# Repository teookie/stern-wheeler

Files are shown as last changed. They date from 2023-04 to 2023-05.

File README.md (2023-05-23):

# stern-wheeler
Filament buffer for multi-material FDM 3D printers

Special Note:
I have uploaded the Stern-Wheeler to printables. This github will remain and I will keep it updated. Please consider downloading from printables however, as I do enjoy earning free prusament. :-) The mini and mega sizes will not be available here and will only be available on printables.

Thank you to everyone who gave feedback and helped with development!

https://www.printables.com/model/472316-stern-wheeler

Change log:
5/22/2023
- Centered bearings in the wheel. The wheel should be (slightly) more stable
- Added a pic of a loaded 6 lane stern-wheeler to PICs folder
- Added parts for a 9 lane version to printables. This has not been tested by me. Keep in mind that more lanes means more friction.

5/10/2023
- Lengthened axel to interface with a pocket added to the cover, and enlarged the spacer to fit around the axel. This improves wheel alignment during assembly, and makes the wheel installation more robust. See section view added to pics below. (I had a situation where the filament spool got jammed causing the extruder to pull the filament hard enough to misalign the wheel. This change is meant to prevent this.)
- Remodeled the wheel-mount so that it overlaps the joint between lane #1 and the wheel. This will prevent the thin wall of lane 1 from deflecting and making a gap where filament can escape.
- Added embossed "F" and "B" to the front and back of the wheel to aid during installation.
- Reversed wheel print orientation - it now prints on it's front face instead of the back face. This prevents possible wheel misalignment caused by drooping filament in the bearing pocket bridges.

To update an existing stern-wheeler with these improvements, print and install the following parts:
- wheel-mount
- axel
- spacer
- cover

5/6/2023
- Published these files at printables.com
- Added mini and mega sizes to printables
- Removed assembly instructions and replaced with an exploded view (a picture is worth 1000 words)

5/4/2023
- Removed ridges from wheel and added scallops. Greatly reduces wheel friction.
- Added a notch to the wheel for the print seam. Make sure your slicer takes advantage! Reduces wheel friction.
- Loosened fit of pins slightly to prevent lane cracking during assembly. 
- Reduced thru hole diameter for 5mm fasteners on axel. Positions wheel more accurately during assembly.
- Rolled back increased clearance between lanes and wheel from 4/7 update. Not needed with new wheel design.

4/7/2023
- Oriented stl's for printing
- Lengthened pins and added matching recesses to clamps, mount, and wheel mount. Should help with wheel alignment during assembly.
- Increased clearance between lanes and wheel by 0.1mm
- Added hex feature to axle that recesses into the wheel mount. Should make assembly easier.
- Removed material from bottom of wheel to make wheel alignment easier
- Made filament path "ambidextrous" so either side can be the inlet or outlet
- Added BOM
- Added written printing and assembly instructions to this readme

BOM
- 2x 608 Bearings
- 12x M3 heatset inserts
- 12x M3x8 or M3x10 cap screws
- 2x M5x16 button head screws
- about 700g of filament (for a 6 lane standard size buffer in ABS)

Printing instructions:
- Designed to be printed with ABS. If you mix materials make sure that they have equal amount of shrinkage or your wheel might not fit!
- 2 perimeters, 15% infill for wheel
- 4 perimeters, 40% infill for everything else

Assembly instructions:
1) See exploded view. ;-)

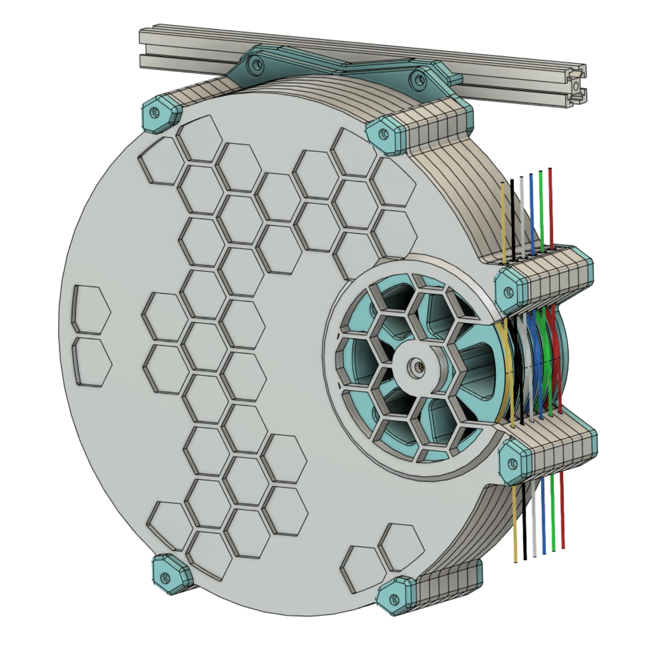
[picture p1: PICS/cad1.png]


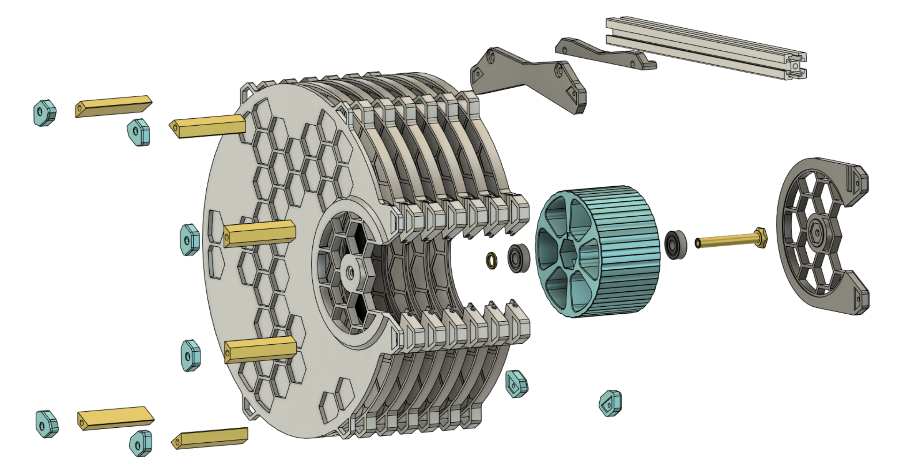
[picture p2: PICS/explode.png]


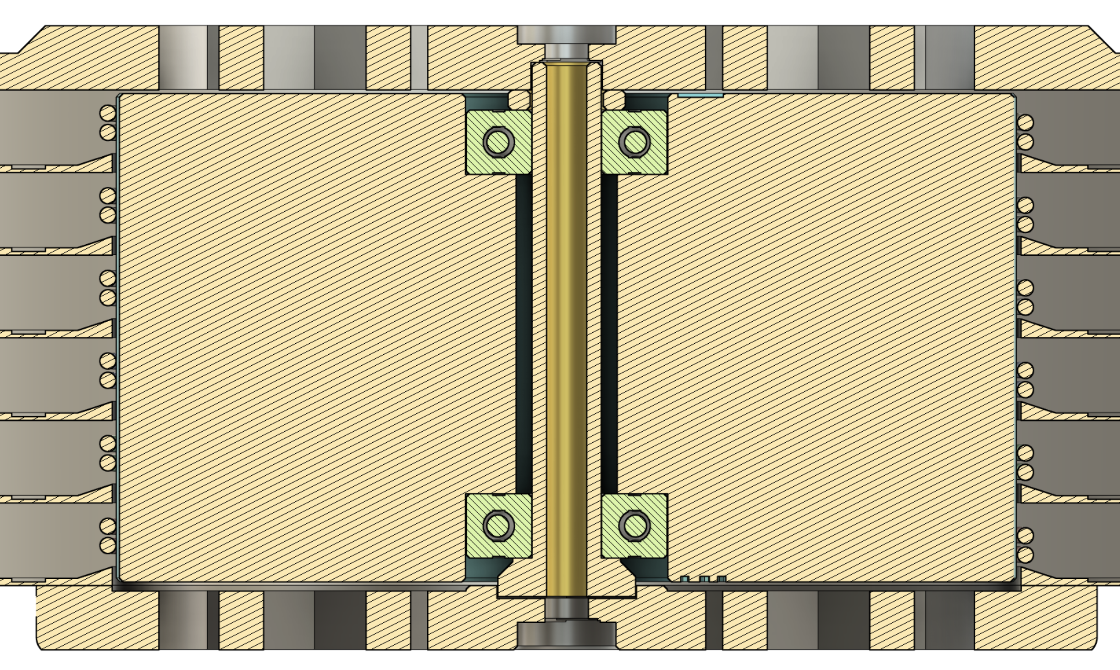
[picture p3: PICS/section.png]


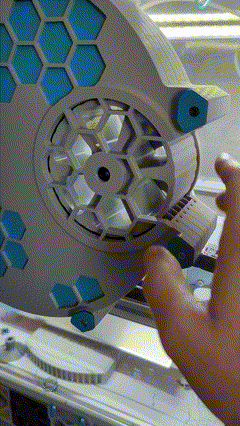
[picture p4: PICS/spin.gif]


https://youtube.com/shorts/Z2WNvIMlSTY?feature=share

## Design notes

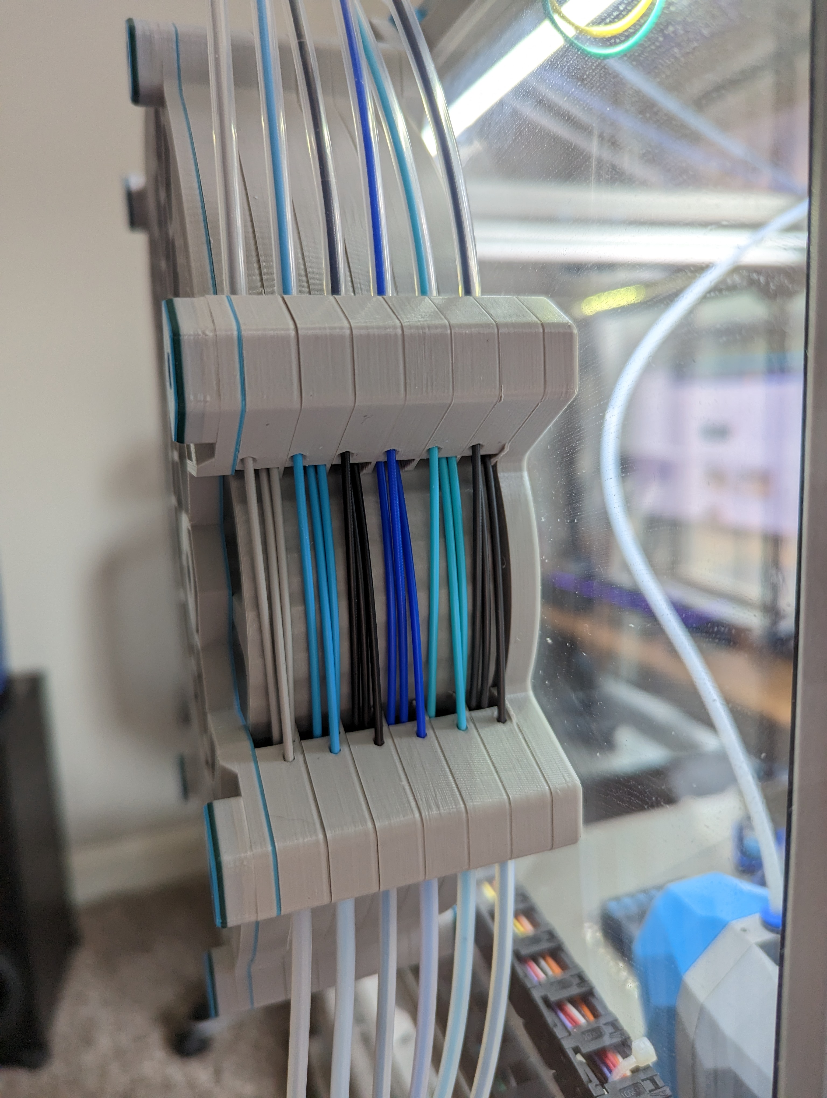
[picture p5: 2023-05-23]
PICS/loaded.jpg

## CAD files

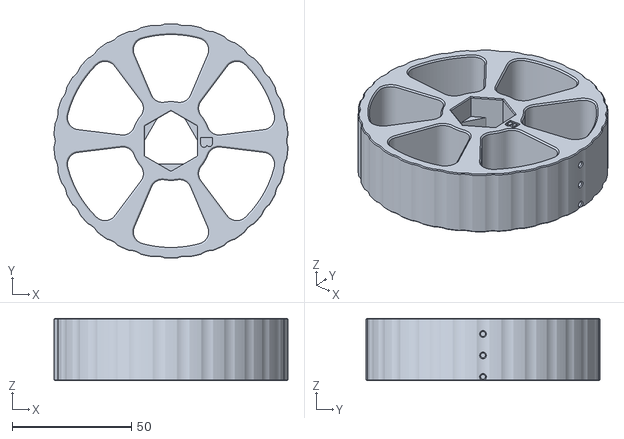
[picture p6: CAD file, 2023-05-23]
STLs/EXPERIMENTAL-tpu-wheel.stl
98.1 x 98.2 x 26.2

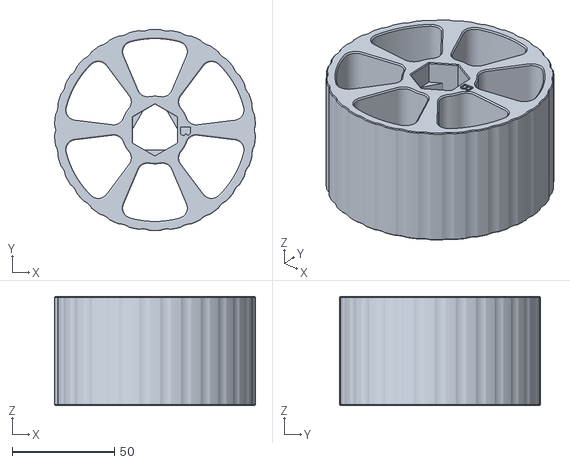
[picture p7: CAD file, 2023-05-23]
STLs/wheel.stl
98.1 x 98.2 x 53.2

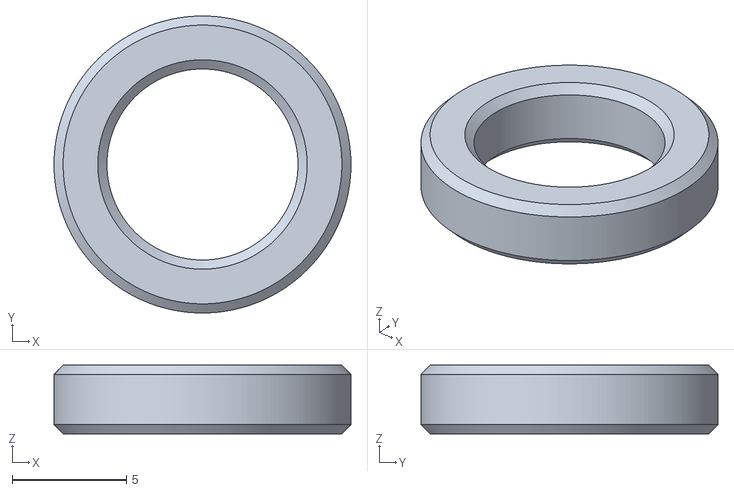
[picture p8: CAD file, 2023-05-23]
STLs/spacer.stl
13.0 x 13.0 x 3.00

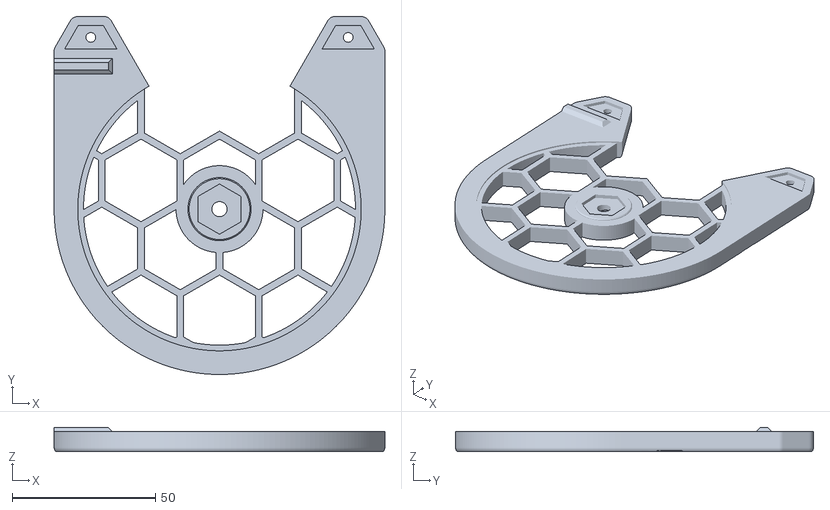
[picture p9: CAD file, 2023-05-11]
STLs/wheel_mount.stl
115.6 x 125.1 x 8.40

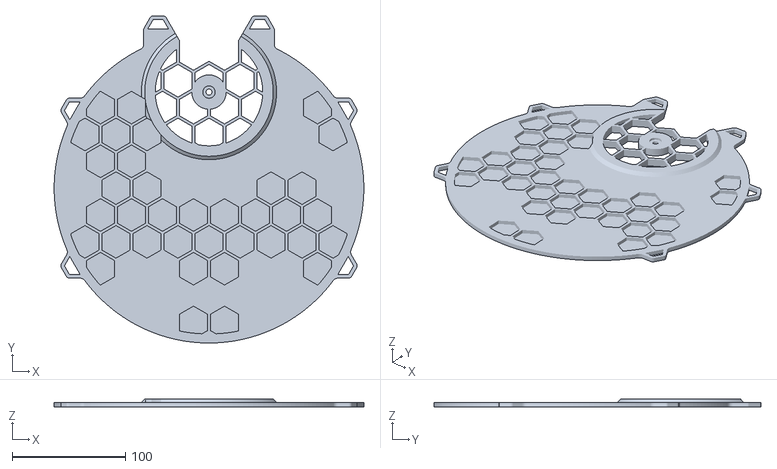
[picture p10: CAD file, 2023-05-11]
STLs/cover.stl
274.0 x 289.3 x 7.00

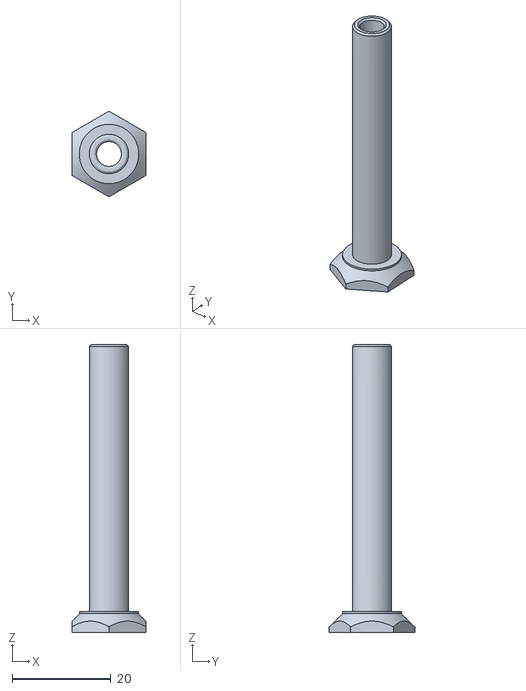
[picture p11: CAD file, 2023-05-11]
STLs/axel.stl
15.0 x 17.3 x 58.2

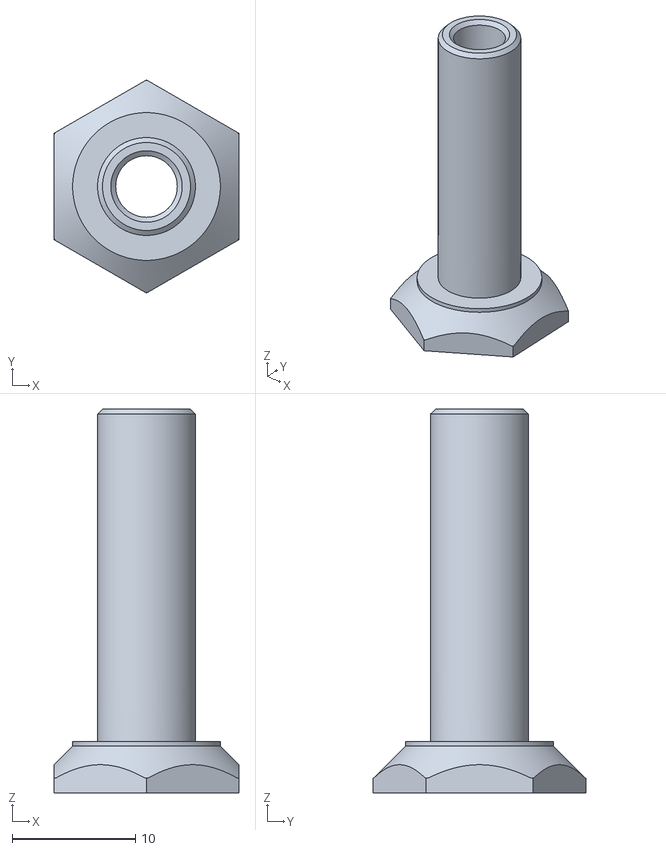
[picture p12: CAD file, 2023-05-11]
STLs/3-lane axel.stl
15.0 x 17.3 x 31.2

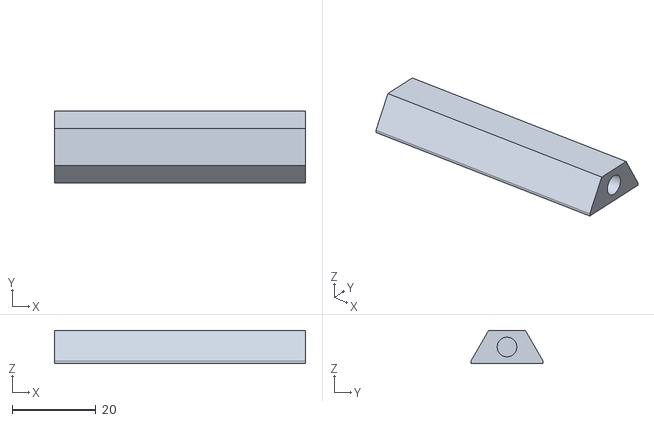
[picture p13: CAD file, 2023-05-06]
STLs/pin.stl
60.0 x 17.3 x 8.00

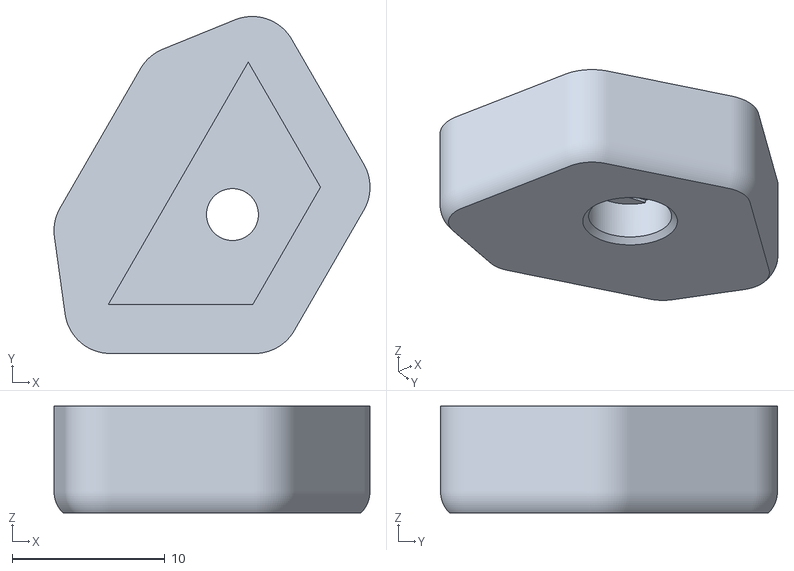
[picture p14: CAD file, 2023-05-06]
STLs/clamp.stl
20.7 x 22.1 x 7.00

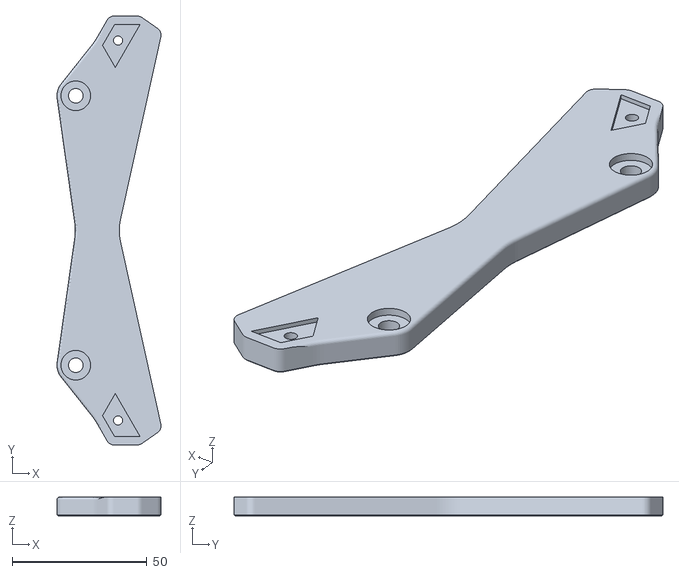
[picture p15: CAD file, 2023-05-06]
STLs/mounting_bracket.stl
38.6 x 159.2 x 7.00

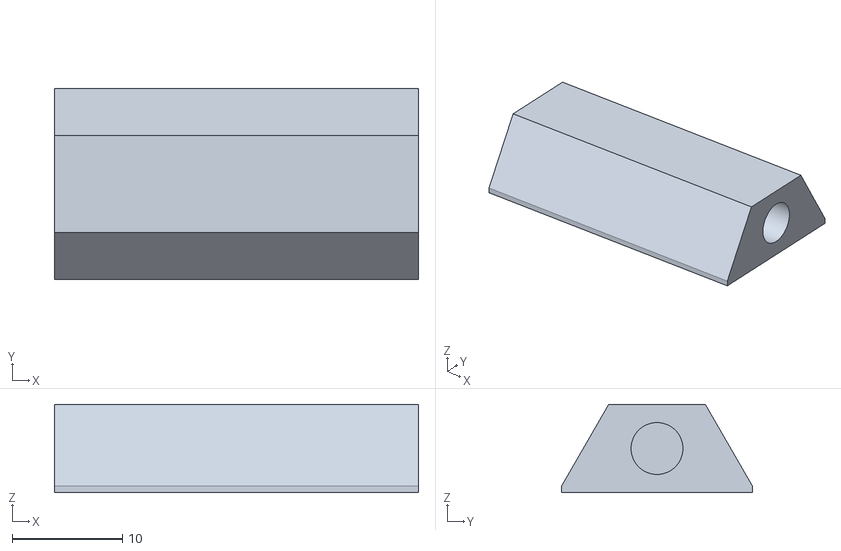
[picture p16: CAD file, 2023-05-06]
STLs/3-lane pin.stl
33.0 x 17.3 x 8.00

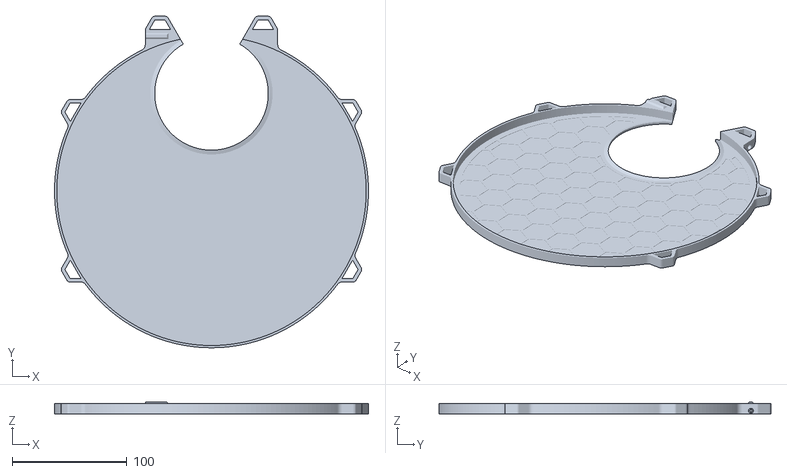
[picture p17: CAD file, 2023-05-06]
STLs/lane.stl
274.0 x 289.3 x 10.4

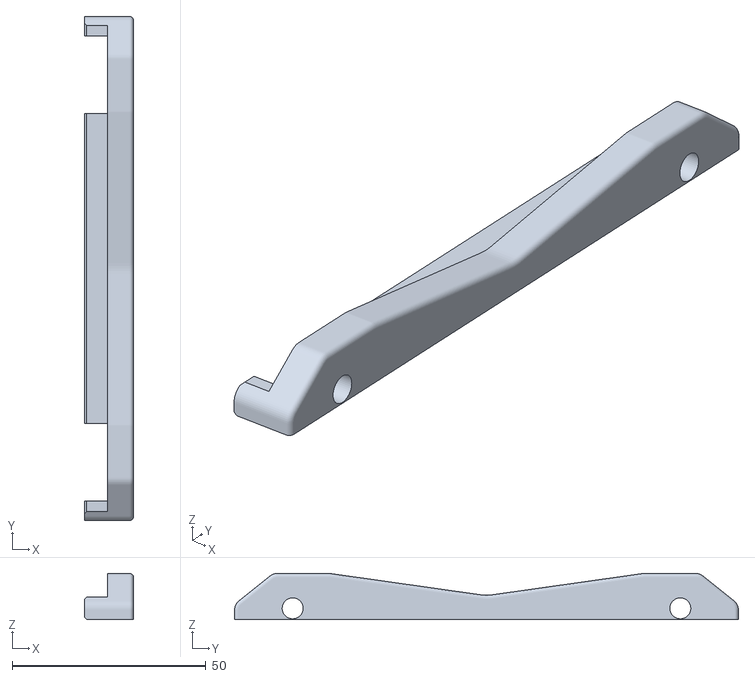
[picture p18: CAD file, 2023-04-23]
STLs/2020_hanger.stl
12.7 x 130.0 x 11.9

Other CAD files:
STLs/3-lane wheel.stl

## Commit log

2023-04-23 added STP and STL files
    [2020_hanger.stl, 3-lane axel.stl, 3-lane pin.stl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]
2023-04-25 Update 3-lane pin.stl
    [3-lane pin.stl]
2023-04-27 improved part fit and ease of assembly
    [2020_hanger.stl, 3-lane axel.stl, 3-lane pin.stl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]
2023-04-30 improved axel and wheel mount printability
    [axel.stl, wheel_mount.stl]
2023-04-30 print orientation
    [axel.stl, wheel_mount.stl]
2023-05-04 updated wheel design
    [3-lane axel.stl, 3-lane wheel.stl, axel.stl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]
2023-05-04 forgot to orient STLs
    [3-lane axel.stl, 3-lane wheel.stl, axel.stl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]
2023-05-06 publish to printables
    [2020_hanger.stl, 3-lane axel.stl, 3-lane pin.stl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]
2023-05-11 added robustness
    [3-lane axel.stl, 3-lane wheel.stl, axel.stl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]
2023-05-23 centered bearings in wheel
    [3-lane wheel.stl, spacer.stl, wheel.stl]
